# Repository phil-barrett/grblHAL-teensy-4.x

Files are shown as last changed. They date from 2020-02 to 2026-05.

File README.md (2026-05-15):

# grbl-teensy-4
GRBL Breakout Boards for Teensy 4.x Uses the [grblHAL Teensy 4 version](https://github.com/grblHAL/iMXRT1062).
# Resources for grblHAL, T41U5XBB and related CNC topics
[Resources](https://www.grbl.org/resources)

## Nov 12, 2025.  V2.20 is now available.
Upgraded to AHCT drivers.
Upgraded to EL3H7 optoisolators.
Added board level configuration to support spindle sync. See [user manual](https://github.com/phil-barrett/grblHAL-teensy-4.x/blob/master/T41U5XBB%20User%20Manual.pdf) for details.
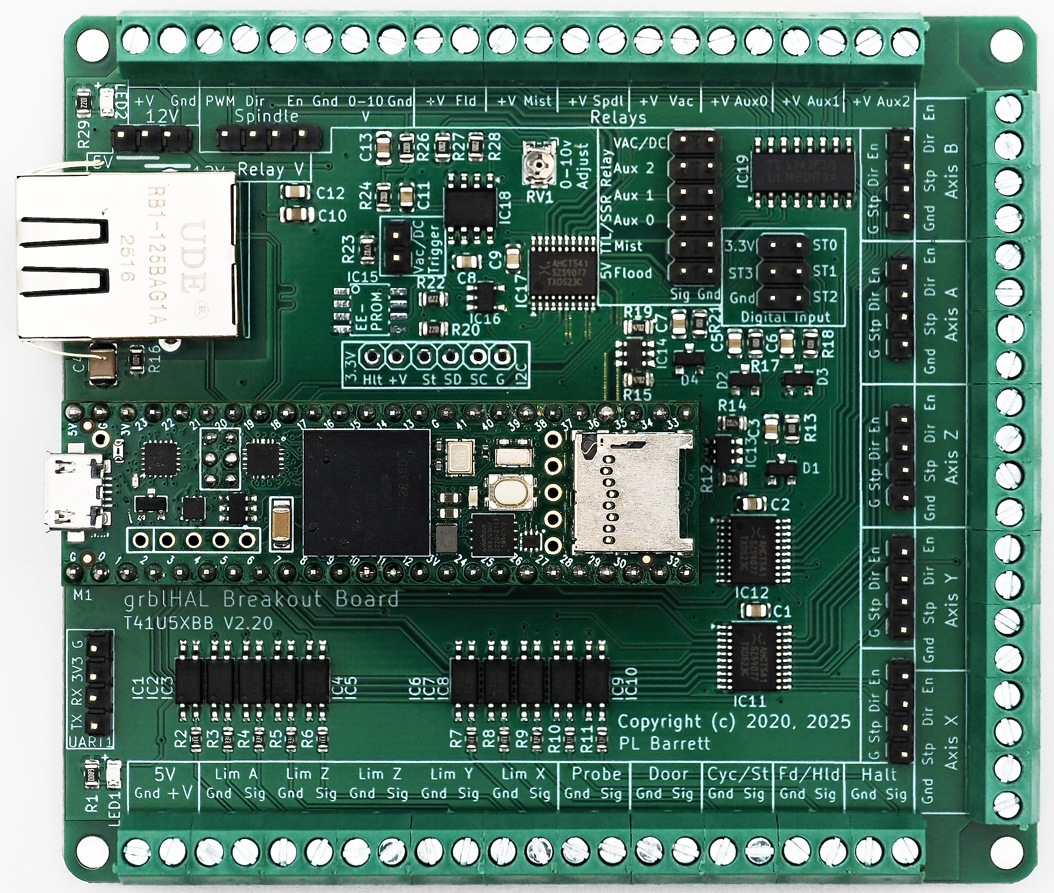
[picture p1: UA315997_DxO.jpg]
.

[Available for purchase on my store.](https://brookwood-design-77.myshopify.com/)

## Aug 20, 2025.  V2.10 is now available.
Trimmer potentiometer moved onto PCB, unneeded features removed and some cosmetic changes.  Now using KiCAD instead of Eagle. V2.11 is coming but is functionally the same as V2.10 (minor slik screen changes).  [User Manual](https://github.com/phil-barrett/grblHAL-teensy-4.x/blob/master/T41U5XBB%20User%20Manual.pdf) updated. 

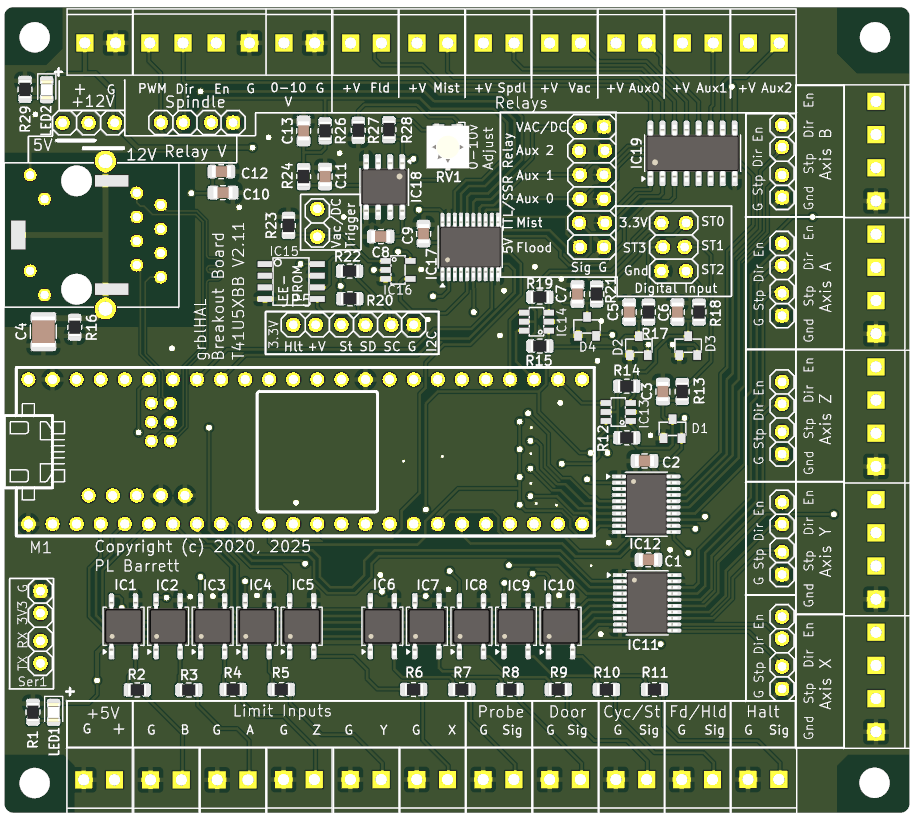
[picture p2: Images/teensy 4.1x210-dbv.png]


## Oct 15, 2020.  V2.09 is now available.
A small number of changes, mostly cosmetic. Also added mounting holes for I2C and Serial I/O daughter boards. 
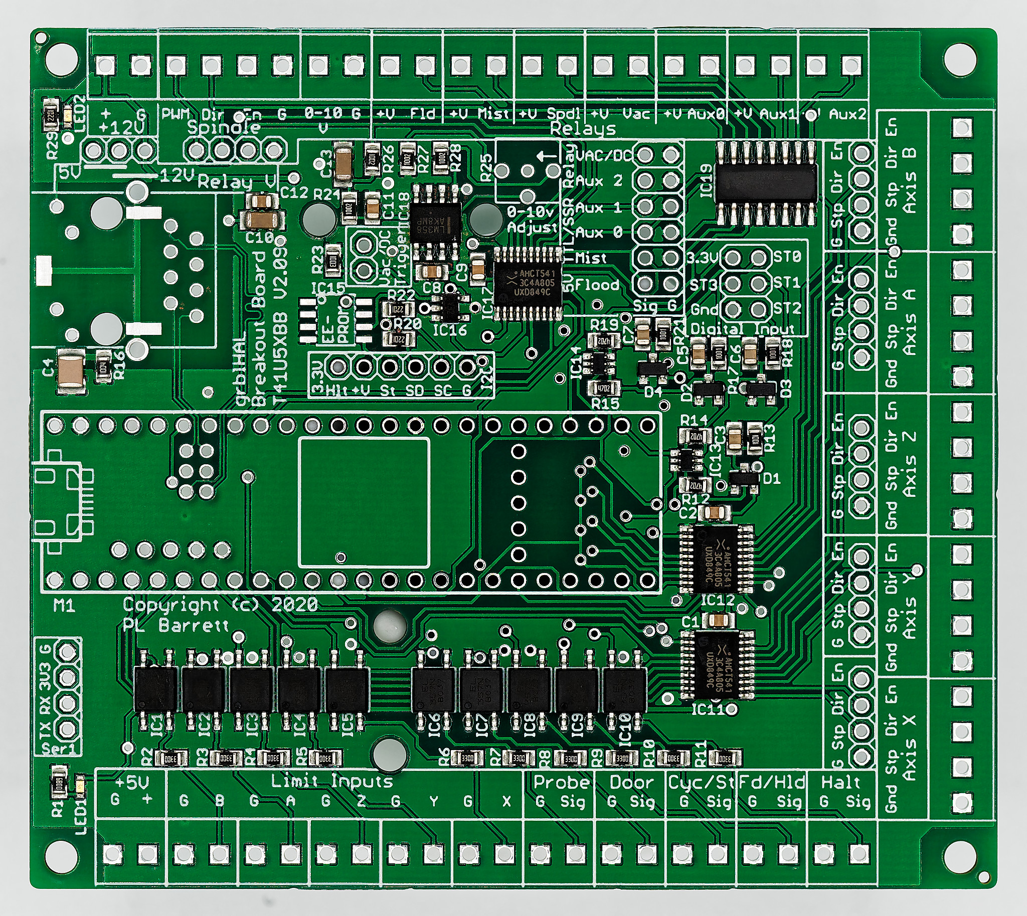
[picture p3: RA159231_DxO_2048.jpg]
T4.1 BreakuoutBoard V2.09 Unkit PCB


## Sept 29, 2020. Ethernet Support Added
grblHAL support for Ethernet is now pretty solid.  I have updated the [User Manual](https://github.com/phil-barrett/grblHAL-teensy-4.x/blob/master/T41U5XBB%20v207.pdf) to include instructions on using Ethernet. 

## June 28, 2020. New Versions!
I have finished 2 new 5 axis versions based on the Teensy 4.1. One supports an Ethernet interface and the other supports a USB interface. I will be making a few "Unkit" boards avalable. These have all the surface mount components installed (with the execption of the EEPROM IC). Teensy 4.1 not included. 

The "Unkit" board.
T4.1 BreakuoutBoard Unkit Version
T41U5XBB - Fully populated USB based version.  
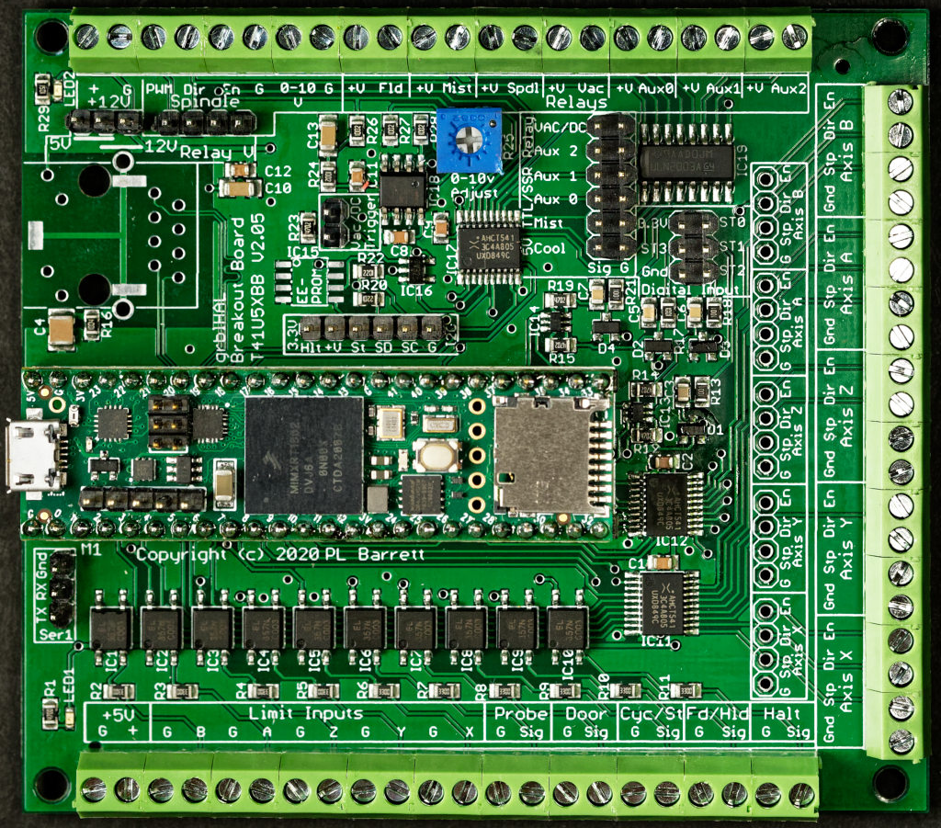
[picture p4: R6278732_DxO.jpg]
T4.1 BreakoutBoard T4.1 USB Breakout Board - T41U5XBB


T41E5XBB - Fully populated Ethernet version
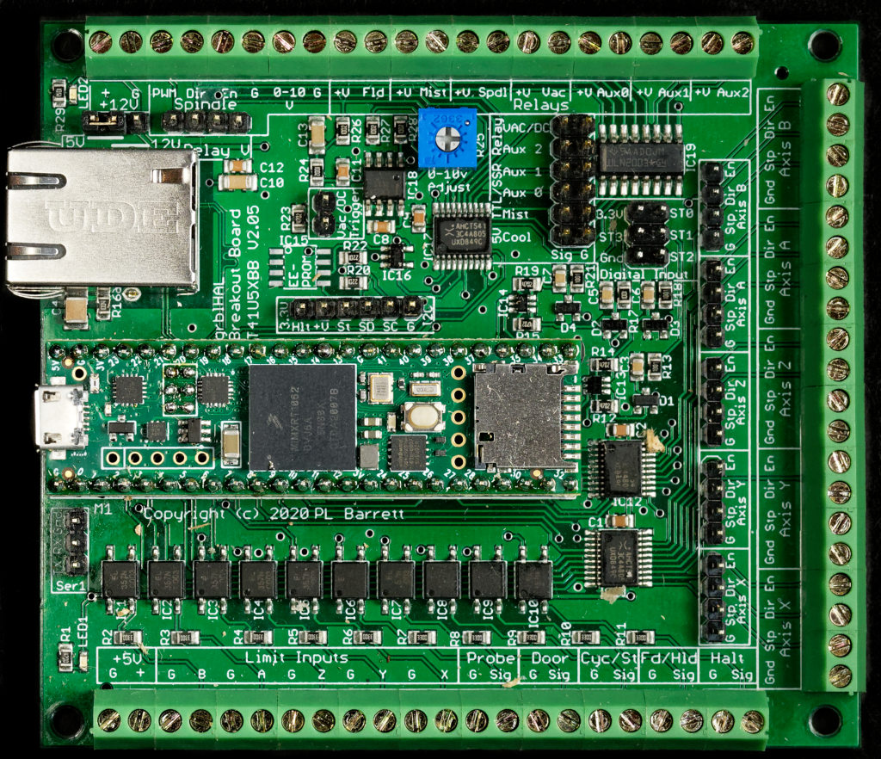
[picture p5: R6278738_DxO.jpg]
T4.1 BreakoutBoard T4.1 Ethernet BreakoutBoard - T41E5XBB


Lots of new features!
## Features
  * 5 Axis control outputs – 5V compatible.
  * Independent enables for each axis.
  * 10 Opto-isolated inputs including standard GRBL controls and limits switches for all axes.
  * 7 Relay Outputs – Spindle, Mist Coolant, Flood Coolant, Dust Collector and 3 auxiliary relays. Each output can control a relay coil directly or 5V TTL (SSR compatible) devices.
  * Dust Extraction relay support. Activated by spindle enable.
  * Separate control of Dust Collector relay via pin header.
  * Relay coil voltage switchable between 5V and 12V. 
  * Standard GRBL spindle control outputs – 5V compliant.
  * 0-10V spindle control output.
  * Screw Terminals for reliable connections available for most I/O.
  * 4 Digital Inputs – EMI protected, 15.9KHz low pass filter, Schmitt Trigger.
  * I2C header.
  * EEPROM footprint for SOIC8 devices.
  * LED indicators for 5V and 12V.
  * USB interface.
  * Ethernet interface. (T41E5XBB only)
  * Serial I/O Header

## Firmware
Prebuilt versions of grblHAL are available to directly load into the Teensy 4.1 [Follow the instructions here.](https://github.com/phil-barrett/grblHAL-teensy-4.x/blob/master/prebuilt.md)

## Documentation
### Schematic
The two versions currently share a common schematic and PCB layout. This may not be the case in the future. [Schematic is here.](https://github.com/phil-barrett/grbl-teensy-4/blob/master/v2.07%20schematic.pdf)

### Manual
The [User Manual is available here.](https://github.com/phil-barrett/grbl-teensy-4/blob/master/T41U5XBB%20v207.pdf)

### Bare PCB from OSHPark
[Available here](https://oshpark.com/shared_projects/QWr3OZUe) This is fairly expensive. For a less costly approach, you can use the Gerber files below to order from more cost effective fabs.

### Gerbers
[Gerbers are available here.](https://github.com/phil-barrett/grbl-teensy-4/blob/master/teensy%204.1x207.zip) Board size is 85 x 96 mm, 2 layer, 1.6 mm thickness.

### Build Guide
A brief guide to building grblHAL from source [for the breakout board is here](https://github.com/phil-barrett/grbl-teensy-4/blob/master/grblHAL%20Build%20Guide.pdf).

## Previous Version
T4 Breakout Board

## Features:
  * 4 Axis control outputs – 5V Compatible.
  * 8 Opto-isolated inputs.
  * Full spindle control outputs – 5V compatible.
  * 0-10V spindle control output.
  * 7 Relay Outputs.
  * Relay voltage switchable between 5V and 12V. 
  * Dust Extraction relay output slaved to spindle.
  * Screw Terminal I/O for reliable connections.
  * I2C header.
  * EEPROM footprint for SOIC8 devices.
  * LED indicators for 5V and 12V.

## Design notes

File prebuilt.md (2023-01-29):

## Prebuilt Firmware

### Prebuilt Firmware depreciated
With advent of the Web Builder, it is very easy to build custom versions of grblHAL firmware.  As such, there is no need for prebuilt versions. We will leave the current files available but highly recommend moving to the [grblHAL Web Builder](http://svn.io-engineering.com:8080/). For more information, take a look at a brief [tutorial on the grblHAL Web Builder](https://www.grbl.org/single-post/using-the-grblhal-web-builder).

### Using the Web Builder
Some Web Builder configuration files are [located here](https://github.com/phil-barrett/grblHAL-teensy-4.x/blob/master/iMXRT1062_T41U5XBB-files.zip). Download and extract the file that reflects your machine. Use the Load Board button to load the .json file. If one does not meet you exact needs, choose the one that is closest and modify it.

Here are the configuration files that are available:

iMXRT1062_T41U5XBB-3X.json - 3 Axis

iMXRT1062_T41U5XBB-3X-qangY.json - 3 Axis, Gang Y

iMXRT1062_T41U5XBB-3X-AutoSqY.json - 3 Axis, Auto-Square Y

iMXRT1062_T41U5XBB-3X-AutoSqY-SDCard-Keypad.json - 3 Axis, Auto Square Y, SDCard, Keypad

iMXRT1062_T41U5XBB-4X.json - 4 Axis

iMXRT1062_T41U5XBB-4X gangY.json - 4 Axis, Gang Y

iMXRT1062_T41U5XBB-4X-AutoSqY.json - 4 Axis, Auto-Square Y

iMXRT1062_T41U5XBB-4X-AutoSqY-SDCard-Keypad.json - 4 Axis, Auto-Square Y, SDCard, Keypad

iMXRT1062_T41U5XBB-5X-SDCard-Keypad.json - 5 Axis, SDCard, Keypad

Depreciated text follows.
### Available Versions
These are found in [configurations.zip](https://github.com/phil-barrett/grblHAL-teensy-4.x/blob/master/configurations.zip).   There are no USB only versions anymore.  These versions all work with USB or Ethernet. At this time, we do not recommend using the compat versions - you should use one of the many GCode Senders that work with grblHAL. If you need compatibility mode and other options, you will need to install the source from github and build it.

"3X qei" - 3 Axis, Aux Relays, Quadrature Encoder

"3X qangY qei" - 3 Axis, Aux Relays, Quadrature Encoder

"3X qangY AutoSq qei" - 3 Axis, Aux Relays, Quadrature Encoder

"3X qangY AutoSq qei SDCard Keypad" - 3 Axis, Aux Relays, Quadrature Encoder

"3X compat" - 3 Axis, no options, compatibility with older senders.

"4X qei" - 4 Axis, Aux Relays, Quadrature Encoder

"4X gangY qei" - 4 Axis, Aux Relays, Quadrature Encoder

"4X gangY AutoSq qei" - 4 Axis, Aux Relays, Quadrature Encoder

"4X gangY AutoSq qei SDCard Keypad" - 4 Axis, Aux Relays, Quadrature Encoder

"4X compat" - 4 Axis, no options, compatibility with older senders.

"5X qei SDCard Keypad" - 5 Axis, Aux Relays, Quadrature Encoder

"5X compat" - 5 Axis, no options, compatibility with older senders.

### Options
nX - number of axes

gangY - Y Motor is ganged with A (if 3 Axis) or B (if 4 Axis)

qei - Quadrature encoder on digital inputs. Supports spindle and feed rate override.

Compat - Sender compatibility.  disables new features of grblHAL and maintains compatibility with senders.

SDCard - SDCard support

Keypad - keypad support

More options will be added in the future.

### Loading Firmware onto a Teensy 4.1
Follow these basic steps:
1. Download the [firmware configurations file](https://github.com/phil-barrett/grblHAL-teensy-4.x/blob/master/configurations.zip) and extract the contents.
2. Select the .hex file that coresponds to the features you will use.
3. Obtain the Teensy Loader for your platform.
4. Use the loader to load the .hex file into your Teensy.

See the platform sections for details and hints.

#### Windows 
Download Teensy.exe from the [PJRC Website here](https://www.pjrc.com/teensy/loader_win10.html). The page may say Windows Vista but it works for all recent Windows versions.
Plug in your Teensy 4.1 via USB. Find Teensy.exe and run it.  It should open as a small window. In File/Open HEX File, select and open the .hex file you want and press OK. Then, press the button on the Teensy 4.1. You are ready to test it now. 

#### Macintosh OS X
Macintosh instructions [are here](https://www.pjrc.com/teensy/loader_mac.html). Plug in your Teensy 4.1 via USB. Follow the instructions to install and run the loader. It should open as a small window. Then, from the File name, choose "Open HEX File" and open the .hex file you want and press OK. Select "Program" from the "Operations" menu, or click the Program button on the tool bar. It should display a brief loading message. You are ready to test it now

#### Linux
Instructions for Ubuntu [are here](https://www.pjrc.com/teensy/loader_linux.html). Other Linux versions work though you will need to build the loader for your platform.  The [instructions and links to the github repository are here.](https://www.pjrc.com/teensy/loader_cli.html)

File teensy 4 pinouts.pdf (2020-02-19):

Teensy 4.0 GRBL Pin Assignment working document V 0.2

Goals:
1. Common Function on TH Pins for easy prototyping/testing. Simple machine should be possible with TH pins only.
2. Less Common Function of SMT “Back Side” Pins
3. Grouping of similar functions on nearby pins to simplify usage and PCB layout.

Issues/questions:
1. No onboard EEPROM. Use EEPROM emulation? How frequently does EEPROM get written? See (alt) Pin assignment.
2. Does USB use Ser 1? Pins need to be reserved?
3. Pin 13 is LED, output only. Currently on spindle enable. Is there a better use for that pin as a diagnostic?
4. Stepper enable is often unused in simple machines. Move that to back side to free up a TH pin?

Standard vs alternate assignment. Most pin assignments are the same for both. Main difference is the use of I2C channels on the through hole pins.
Through Hole Pins
Pin | Standard assignment | Alternate assignment
0 | Reserved RX1 | Reserved RX1
1 | Reserved TX1 | Reserved TX1
2 | Step X | Step X
3 | Dir X | Dir X
4 | Step Y | Step Y
5 | Dir Y | Dir Y
6 | Step Z | Step Z
7 | Dir Z | Dir Z
8 | Step A | Step A
9 | Dir A | Dir A
10 | Stepper Enable 0 | Stepper Enable 0
11 | Spindle Dir | Spindle Dir
12 | Spindle Enable | Spindle Enable
13 LED | Spindle PWM | Spindle PWM
14 | Reset/Abort | Reset/Abort
15 | Probe | Probe
16 I 2C 0 | Feed/Hold | I2C SCL ch 0
17 I 2C 0 | Cycle Start | I2C SDA ch 0

18 I 2C 1 | Mist Enable | I2C SDA ch 1
19 I 2C 1 | Flood Enable | I2C SCL ch 1
20 | Lim X | Lim X
21 | Lim Y | Lim Y
22 | Lim Z | Lim Z
23 | Lim A | Lim A

Back Side SMT Pins
Pin | Function assignment | Alternate assignment
24 I2C 2 | I2C SCL ch 2 | Feed/Hold
25 I2C 2 | I2C SDA ch 2 | Cycle Start
26 | Step B | Step B
27 | Dir B | Dir B
28 | Lim B | Lim B
29 | Door | Door
30 | Stepper Enable 1 | Stepper Enable 1
31 | Relay 5 | Relay 5
32 | Relay 6 | Relay 6
33 | GPIO 1 | Relay 7
34 | Stepper Enable 2 | Stepper Enable 2
35 | Stepper Enable 3 | Mist Enable
36 | Stepper Enable 4 | Flood Enable
37
38
39

Simple Machine Definition

This section defines the functions needed to build a simple CNC/Laser machine. The goal is to be able to do this only with through hole pins. This allows easy prototyping and testing.

Note that strictly speaking, Stepper Enable is unnecessary and Feed/Hold, Cycle Start are often omitted in basic machines. For Lasers, I believe Spindle pins are used for control.

Step X | Stepper Enable 0 | Lim Y
Dir X | Spindle PWM | Lim Z
Step Y | Spindle Enable | Lim A

Dir Y | Reset/Abort | Feed/Hold
Step Z | Probe | Cycle Start
Dir Z | Lim X

Note this is somewhat stating the obvious but I think it worthwhile to have written down.

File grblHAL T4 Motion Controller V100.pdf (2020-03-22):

## grbl/HAL Teensy 4.0 Motion Controller

V1.00

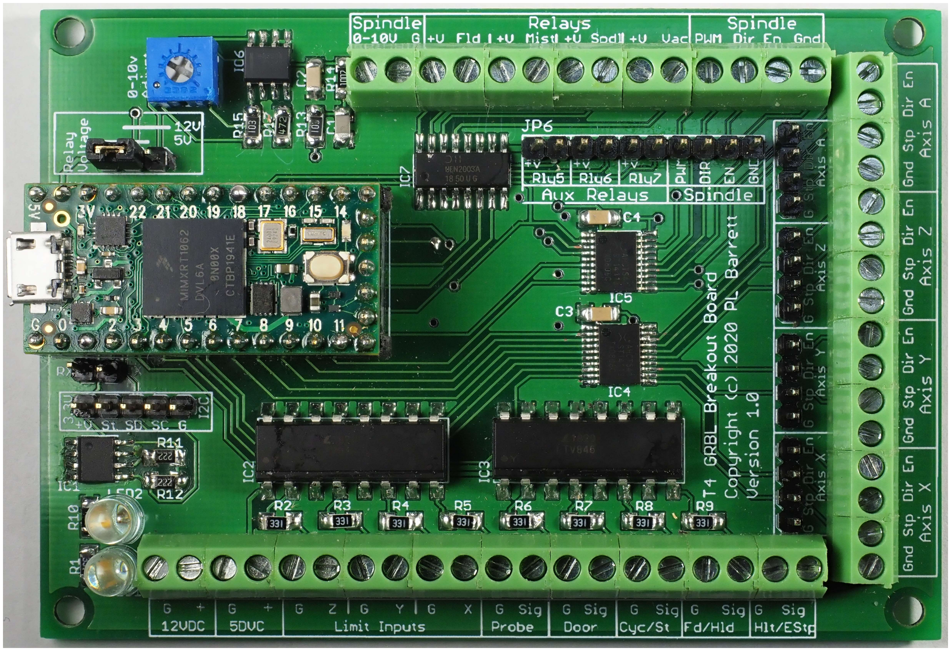
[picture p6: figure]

This document describes V1.00 of the grbl/HAL Teensy 4.0 Motion Controller.

### Features:

- 4 Axis control outputs – 5V Compatible.
- 8 Opto-isolated inputs.
- 7 Relay Outputs.
- Relay voltage switchable between 5V and 12V.
- Screw Terminal I/O for reliable connections.
- I2C header.
- EEPROM footprint for SOIC8 devices.
- Full spindle control outputs – 5V CMOS compatible.
- 0-10V spindle control output.
- Dust Extraction relay output slaved to spindle.
- LED indicators for 5V and 12V.

Stepper Driver outputs.
There are 4 sets of standard GRBL stepper driver outputs: X, Y, Z and A axes. Each has 3 pins: step, direction and enable. Each are 5V compatible and capable of driving opto-isolated stepper driver inputs. Each axis has a set of screw terminals as well as pin headers (0.1”/2.54mm spacing).

Limit Pins.
There are X, Y and Z opto-isolated limit pins available via screw terminals.

Input Pins.
Standard GRBL input pins are supported via screw terminals: Feed/Hold, Cycle/Start, Halt/Stop and Safety Door open. These are opto-isolated.

Copyright © 2020 P. L. Barrett

Probe Input
Probe input is opto-isolated and is available via screw terminals.

Spindle Control.
Screw terminal and pin header outputs for Spindle Enable, Spindle Direction and PWM signals. These are 5V CMOS logic compatible. There is a relay output for the spindle. See Relay section for more details. In addition, 0-10V output for spindle control is provided via a screw terminal.

Relay outputs.
Standard GRBL Flood and Mist relay outputs are supported via screw terminals. Spindle relay output via a screw terminal is supported and controlled by Spindle Enable. In addition, a separate screw terminal relay output for Dust Collection is slaved off the Spindle Enable output.

3 additional relay outputs are supported via pin headers and used via M62-M65 grbl/HAL pin control.

All relay outputs are capable of directly driving relay coils. Each relay driver is capable of up to 100 mA. All 7 are limited to 500 mA in total though above 250 mA, forced air cooling is recommended.

All relays drivers have open collector outputs.

Relay voltage is selectable between 5 and 12V via pinheader labeled Relay Voltage in the upper left corner of the PCB.

I2C Header
An I2C header is provided. 3.3V only, there is no translation to/from 5V. In addition a strobe line from Teensy 4.0 pin 33 is provided on the header. Currently, only a limited number of devices are supported. Check the grbl/HAL github site for more details.

### PCB Assembly

Not all components are required. See Optional Components section for more information.

Assemble the PCB in the following order:
1. Use a flux pen on all pads.
2. Solder the smallest SMD components first – resistors, capacitors.
3. SMD ICs next. Take care with IC4 and IC5 when soldering. Draw the soldering iron along the legs, not perpendicular to them as they easily bend.
4. Now is a good time to verify that all leads are properly soldered. Visual inspection with a magnifier is a good idea. Electrical continuity testing is very helpful – leads that look OK are sometimes not.
5. Mount and solder trimmer resistor R16 and the LEDs next. LED anode goes towards the top of the board (cathode connects to resistor). Trim excess leads.
6. Install the Teensy 4.0 – sockets or actual T4 with headers. See Teensy 4.0 Mounting Options for more information. Now is a good time to test the board before the headers and terminals are installed, making changes harder.
7. Mount and solder any pin headers that you will be using. See diagram xxx for options. Use tape to hold them in place while soldering. Solder an end pin and then adjust for proper alignment. Finish by soldering the rest of the pins.
8. Mount and solder screw terminals. Assemble a complete row, insert and solder an end pin. Then solder the pin at the other end, making sure the row is properly aligned. Then solder remaining terminals while ensuring that the row is straight.

Optional Components.

Many components are optional. Refer to the following diagram.

Notes:
- RX, TX and I2C headers are optional. Install if you need to use an alternate USB connection. Grbl/HAL will work correctly without either header installed.
- EEPROM is optional, Install if you need to use an external EEPROM. Grbl/HAL will work correctly without it.
- Power indicator LEDs are optional. Useful to see if you have power. Grbl/HAL will work correctly without it.
- 0-10V Spindle control is optional. Use if you are using a VFD controlled spindle. Grbl/HAL will work correctly without it if you are manually controller your spindle. We recommend installing the screw terminals as they are hard to add later.
- Relays are optional. The grbl/HAL Teensy 4 Motion Controller is capable of driving relay coils directly. It is recommended that you install the screw terminals even if you don't initially plan on using them. Installing later can be difficult. See note on Vacuum/Dust Collector relay below. But, Grbl/HAL will work correctly without any relays.
- A Axis is optional if you don't have one in your CNC machine.
- Safety Door alarm. Install if you have an enclosure for your CNC machine with a Safety Door sensor. See note about backside pins in the Teensy 4.0 mounting options section below. Grbl/HAL will work correctly without it but see Testing section for disabling the alarm.

### Teensy 4.0 Mounting Options

The Teensy 4.0 comes with 3 sets of pins:
- The T4 has through holes around the perimeter. Typically header pins are soldered into them. The best way to ensure the pins are soldered in straight is to insert them into a solderless breadboard, place the Teesny 4.0 on top of them and solder in place. Take care when prying the assembly off the breadboard. The Teensy 4.0 should like the picture below.
- There is a set of SMD pads for pins 24 through 33 on the bottom. PRJC calls them Backside Pins. We recommend you not bother with them unless you are using a Safety Door Open Sensor, Relays 5 through 7 or the I2C header. If you wish to use them, there are surface mount pin headers that will work. These are difficult to solder because there a number of 402 SMD components close by and it is easy to knock them off. The author of this document has a dead Teensy 4.0 to prove that point. It is possible to use pogo pins though this has not been tested.
- The 3rd set of SMD pads, pins 34 through 39, are unused.

Mounting the Teensy 4.0 on the grbl/HAL Motion Controller PCB can be done in one of two ways:
- Solder directly. This is more reliable though commits the Teensy 4.0 to this application. Install pin headers as shown below and then insert the assembly in place on the PCB and solder. This is the recommended approach to ensure reliability.
- Use pin sockets. These are generally reliable but in a high vibration environment can shake loose. Ensure that the pin headers are installed on the Teensy 4.0 as shown in the picture below. Place the sockets on the Teensy 4.0 (with the headers pins installed) and then insert into the PCB for soldering. Using tape to hold the Teensy 4.0 assembly in place, solder 1 pin at the end of each row, check the alignment and adjust as necessary. Once you are satisfied with the alignment, solder all the pins in place.

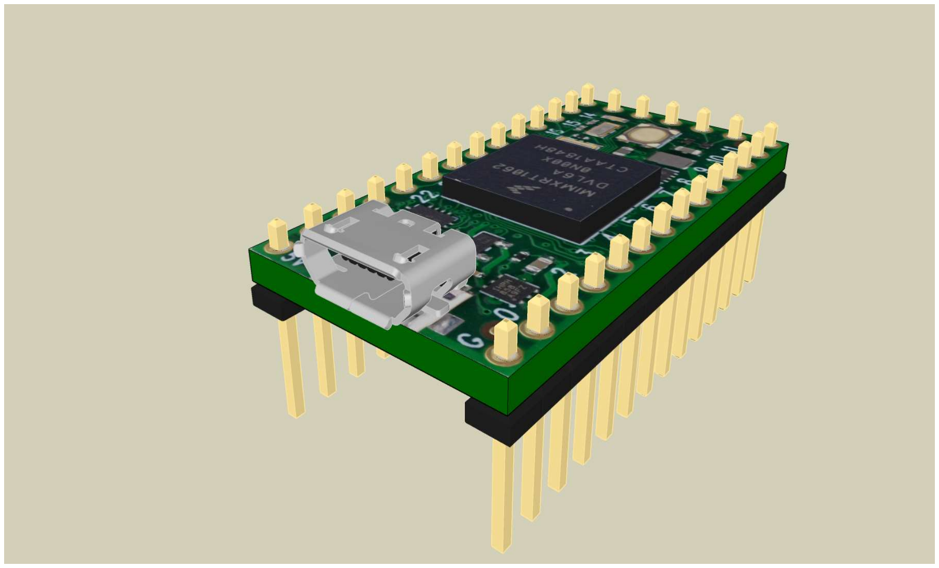
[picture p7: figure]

### Relay Voltage

Relay Voltage source is selectable between 5V fed by the USB host and 12V (or higher) provided via an external power supply. Use a “suitcase jumper” as indicated on the PCB to select the desired voltage. Note, if using more than 2 relays at 5V, we recommend you use an external 5V supply. To do so, you must disconnect VUSB feed on the Teensy 4.0. On the bottom side of the Teensy 4 in the upper right hand corner, when looking at it from the bottom, there is a trace to be cut. That separates Vin from the USB cable and allows 5V input via the screw terminal. See the info card that comes with the Teensy 4.0 or PJRC.COM for more information.

Relay coil voltage up to 48V is permissible and is applied at the input terminal labeled 12V. If using higher than 12V, we recommend changing resistor R1 to limit LED current to below 10 mA. For 24V, use 2.2K Ohm and, for 48V, use 4.7K Ohm. The user is responsible for ensuring that all relays are rated for the voltage they provide.

### Dust Extractor/Vacuum Control

An additional relay driver is provided to drive a dust extractor relay. It is slaved to the Spindle Relay – both are energized when the spindle is turned on (M3). In addition, this relay can be separately and independently controlled by a switch that connects the terminal labeled Vac to ground. The switch must be rated for 200 mA or more. This makes it easy to do clean up with the same shop vac used for dust extraction.

### Loading grbl/HAL

A prebuilt binary is available on github at https://github.com/phil-barrett/grbl-teensy-4. One can also download the source code at https://github.com/terjeio/grblHAL and build it.

### Testing

Your grbl/HAL Teensy 4.0 based Motion Controller is ready to be tested. Attach it to a PC via a USB cable and run a compatible GRBL sender application. We recommend this one: https://github.com/terjeio/Grbl-GCode-Sender Check for the most recent release.

Note, it you don't attach any switches, the system will come up in the alarm state. This is normal. If you are not using the Safety Door Alarm, in the Settings: Grbl tab, Invert control pins section, check the Safety Door box. This makes the system see the (nonexistant) Safety Door as closed.

### 0-10V output setup

The 0-10V circuit works by using an opamp to filter a 3.3V PWM signal and amplify it to 10V. As such it needs 12V input which the user must provide. A second order filter with an aggressive low pass cut off frequency is used to provide a stable signal for the spindle controller.

Because source voltage level can vary, the gain of the op amp must be adjusted. To adjust:
- In the Settings: Grbl tab, set $30, Maximum Spindle Speed, to 1000.
- Send the following command to GRBL: M3 S1000. This turns on the spindle and causes the speed to be set to 100%. The LED on the Teensy 4 should light up.
- Connect a Volt Meter to the 0-10V output and G terminals.
- With a screwdriver, turn R16 until the voltage is as close to 10V as you can get. Anything in the range 9.990V to 10.010V is acceptable.

### Errata:

1. Silk screen legends for Relays 5 and 7 are reversed.
2. The TX, RX header is lacking a ground. Use one of the other terminals or pins marked Gnd or G if you wish to use serial I/O. Grbl/HAL doesn't use it though.
3. Silk screen marks for LED's Anode are missing.

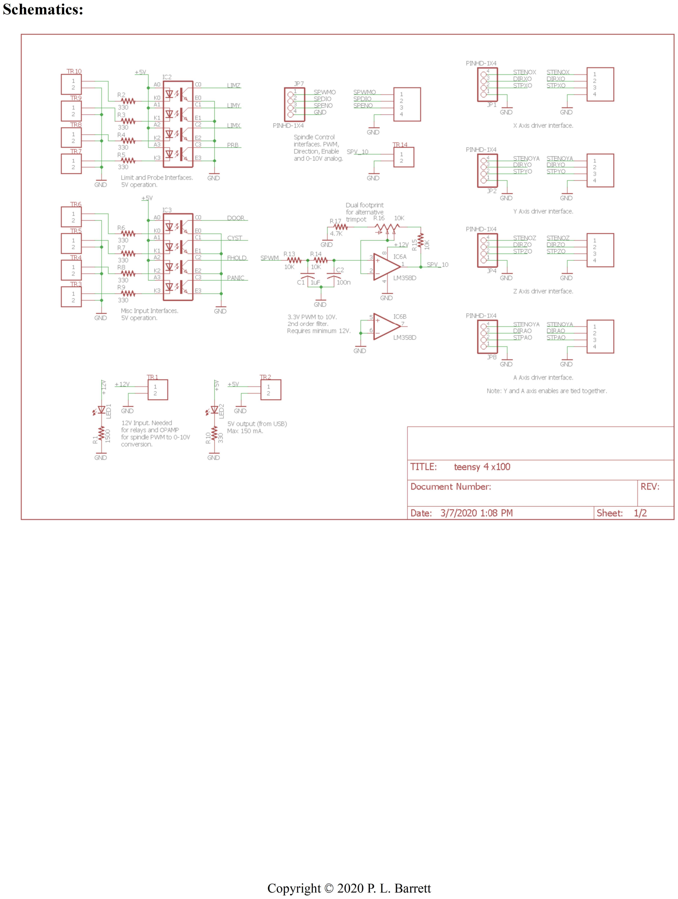
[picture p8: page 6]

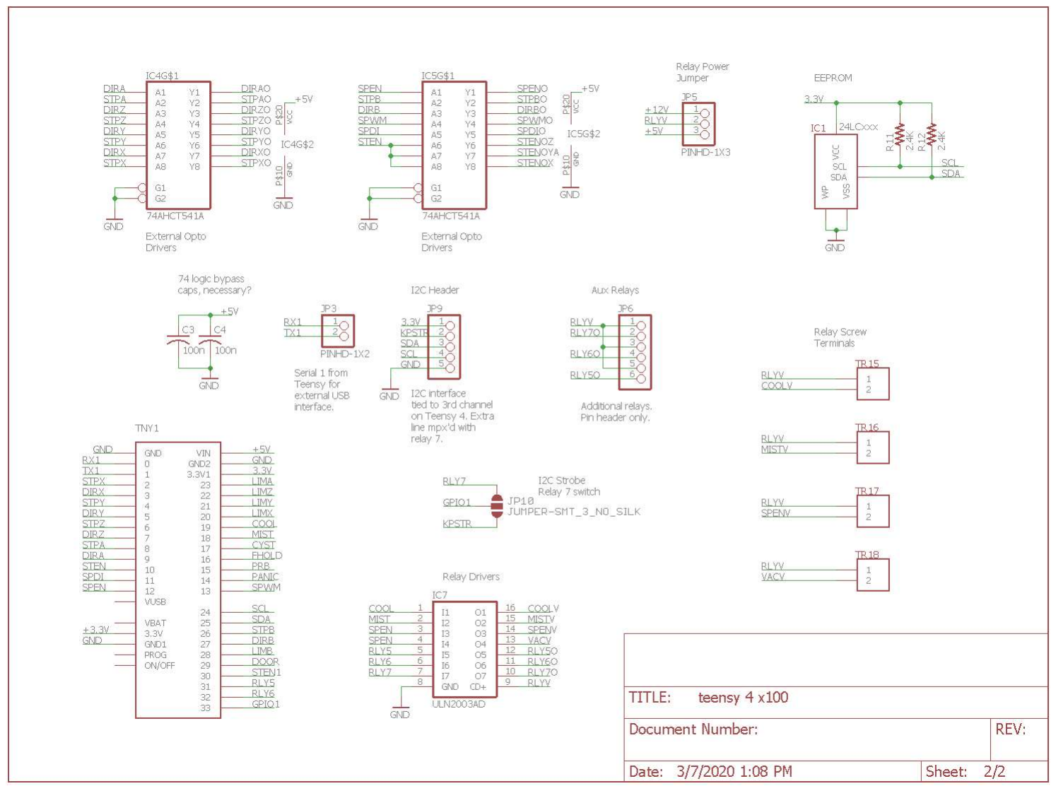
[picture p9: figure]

### Bill of Materials

Notes:
- The PCB has a dual footprint for the10K trimmer potentiometer and will accept 2 different footprints: 3 pins in a row with 0.1”/2.54 mm pitch or a triangular layout with the middle pin offset by 2.54 mm. The first footprint is used by more expensive multiturn trimmers and the second is very common and low cost. The BOM has the lower cost version. Also, you could use a 2K trimmer in place of the 10K.
- 3.5mm pitch screw terminals are fairly common and can be purchased from ebay/amazon/banggood/ali express.
- Pin headers are readily available from the same sources.
- Single row sockets are also readily available from the same sources though good quality ones are not that expensive. We recommend you use good quality sockets.
Part | Value | Number Package | Mouser Part Number | Cost | Unit total | notes
C1 | 1uF 25VDC | 1 | 1206 | 791-1206F105Z250CT | $0.10 | $0.10
C2 – C4 | 100n 25VDC | 3 | 1206 | 710-885012208058 | $0.11 | $0.33
IC1 | 24LC16 | 1 | SOIC-8 | 579-24LC16BT-E/SN | $0.34 | $0.34
IC2 – IC3 | LTV846S | 2 | DIL16-SMD | 859-LTV-846S | $0.68 | $1.36
IC4 – IC5 | 74AHCT541A | 2 | TSSOP20 | 771-74AHCT541PW-T | $0.40 | $0.80
IC6 | LM358D | 1 | SOIC-8 | 595-LM358ADRG4 | $0.36 | $0.36
IC7 | ULN2003AD | 1 | SO16 | 621-ULN2003AS16-13 | $0.48 | $0.48
LED1, LED2 | Green | 2 | LED, TH, T-1 (3 mm) | 859-LTL-4232 | $0.12 | $0.24
R1 | 1500 | 1 | 1206 | 660-RK73B2BTTD152J | $0.10 | $0.10
R2 – R10 | 330 | 9 | 1206 | 660-RK73B2BTTD331J | $0.10 | $0.90
R11 – R12 | 2.4K | 2 | 1206 | 660-RK73H2BTTD2401 | $0.10 | $0.20
R13 – R15 | 10K 1% | 3 | 1206 | 660-RK73H2BTTD1002F | $0.10 | $0.30
R16 | 10K trimmer | 1 | multiple | 3362P-1-103LF | $1.02 | $1.02 cheaper available
R17 | 4.7K 1% | 1 | 1206 | 660-RK73H2BTTD4701F | $0.10 | $0.10
TNY1 | 1 | TEENSY4.0 | $19.95 | $19.95 pjrc.com
Pinheaders | 36 | 2.54mm/0.1” pitch | varies | 0 multiple sources
TR1 – TR20 | screw terminal 25 | 3.5mm Pitch 2 pin | varies | 0 multiple sources
Total | $26.58
Sockets for Teensy | 2 | 14 pin 2.54mm pitch | 437-8018701410001101 | $1.20 | $2.40
Sockets for Teensy | 3 | 5 pin 2.54mm pitch | 437-8018700510001101 | $0.49 | $1.47
Backside Pin Header | 1 | 5x2 pin 2.54mm pitch | 571-5-146131-4 | $1.28 | $1.28

If not using backside pins, you only need 2 14 pin and one 5 pin sockets.

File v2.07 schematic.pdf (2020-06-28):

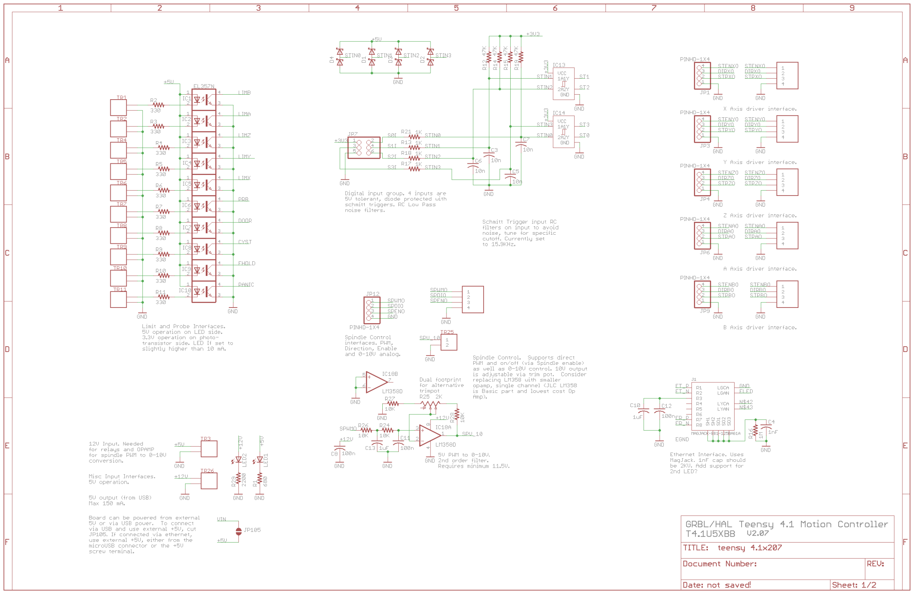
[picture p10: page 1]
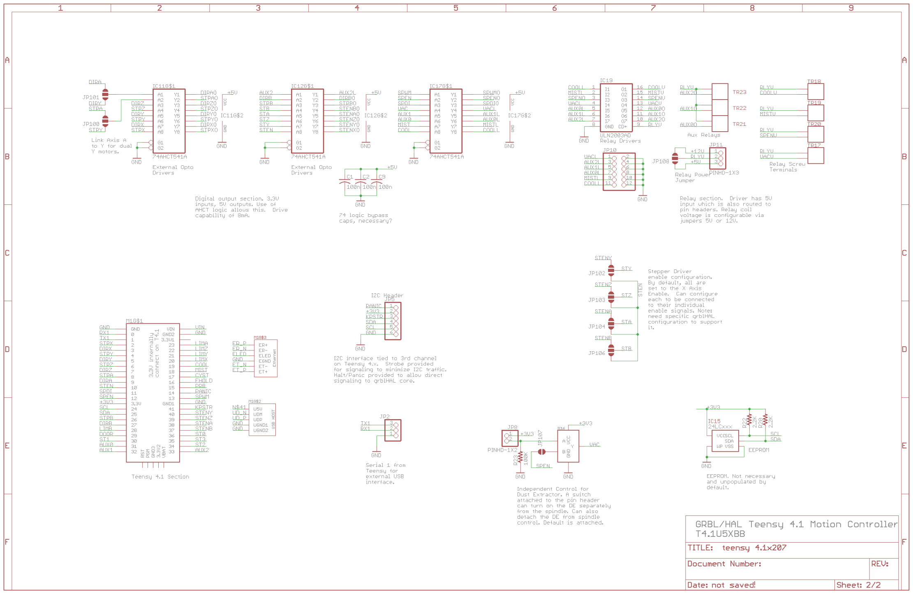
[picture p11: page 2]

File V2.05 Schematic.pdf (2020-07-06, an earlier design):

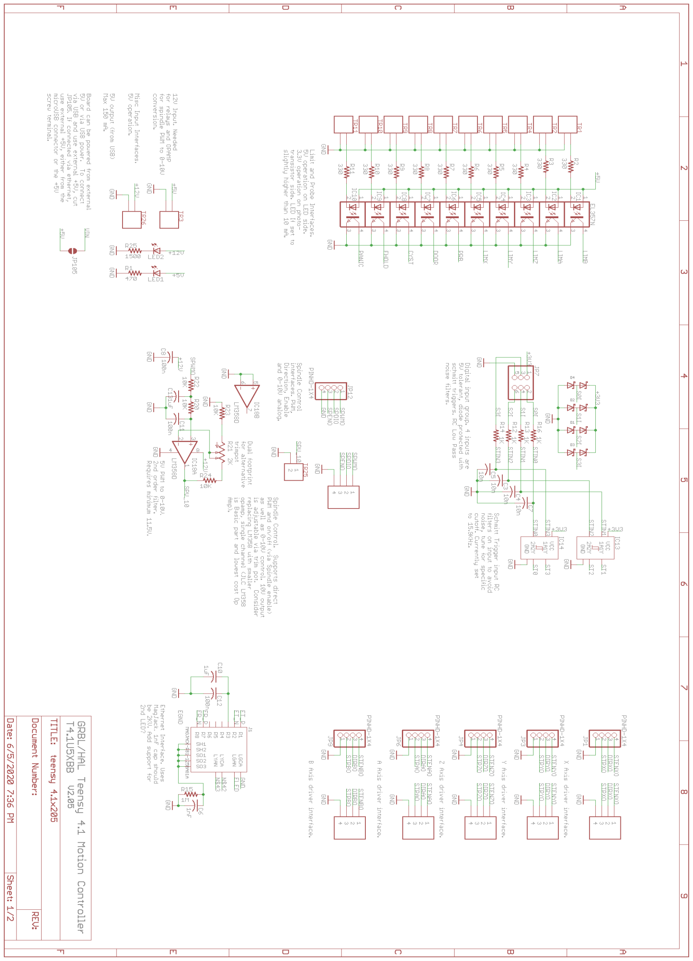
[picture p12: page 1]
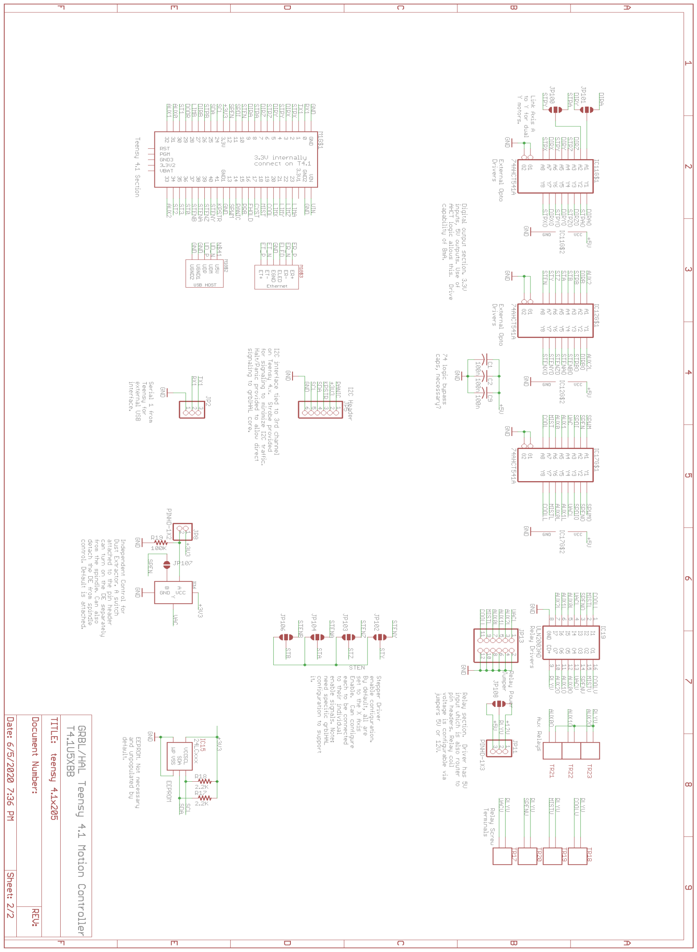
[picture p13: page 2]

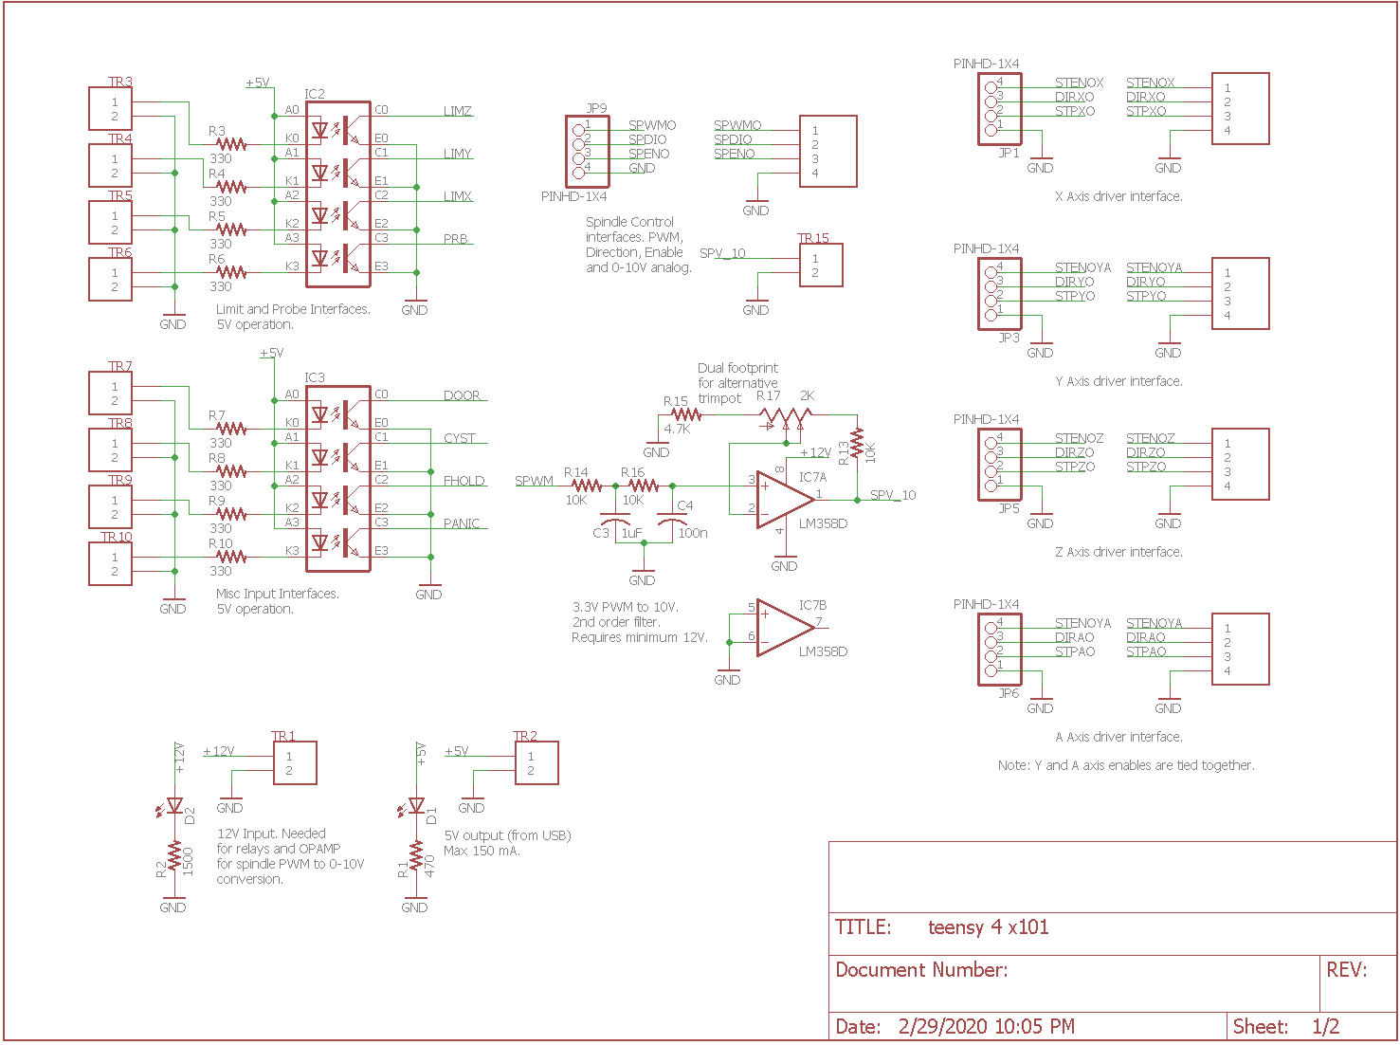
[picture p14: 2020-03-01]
schematic 1 of 2.png

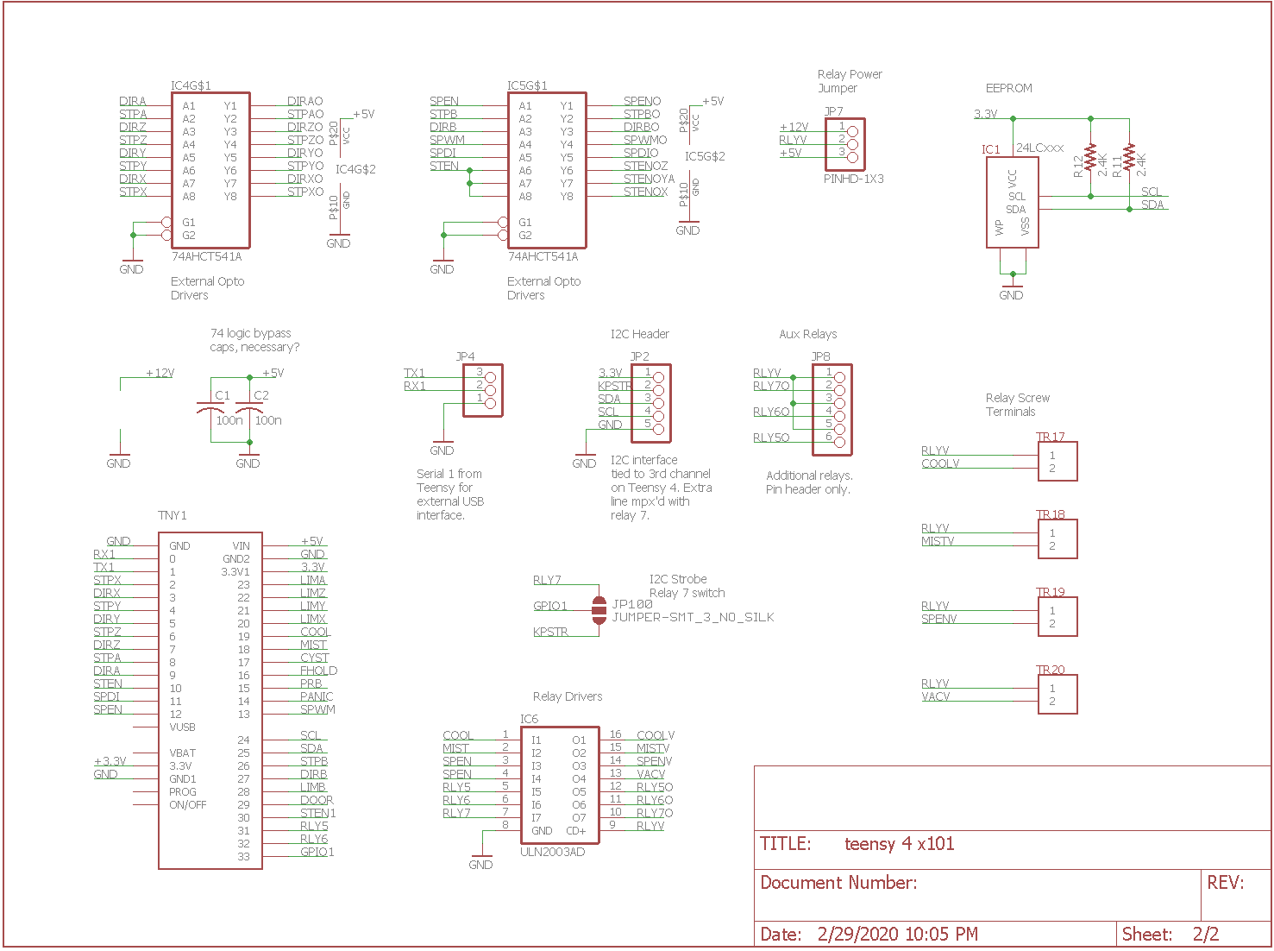
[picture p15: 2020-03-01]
schematic 2 of 2.png

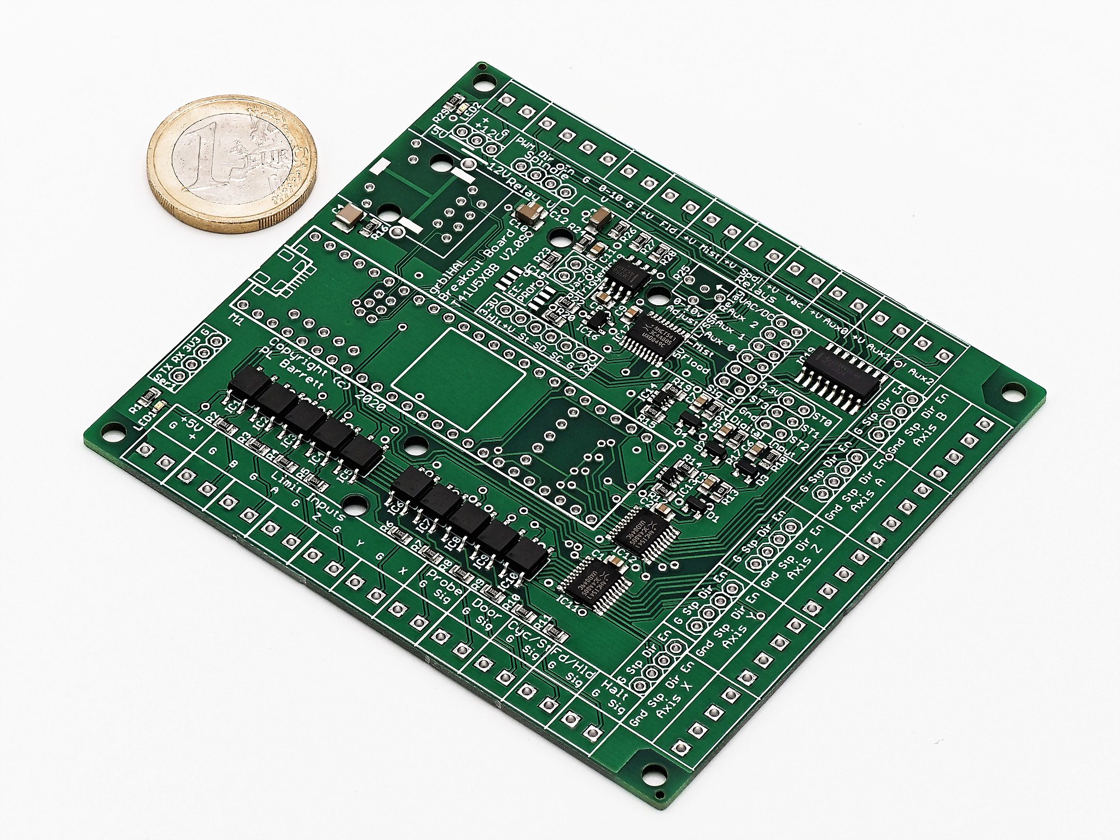
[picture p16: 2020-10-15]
RA159259_DxO_2048.jpg

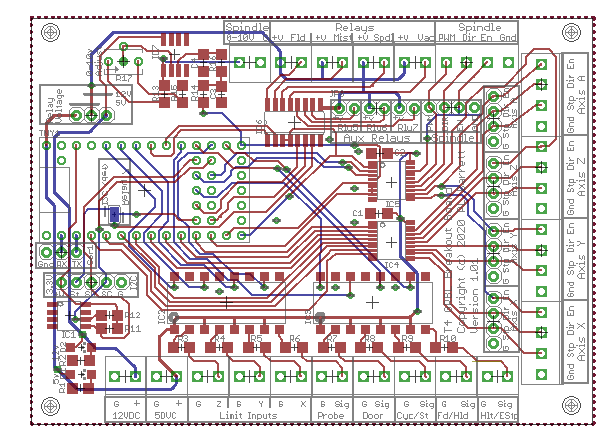
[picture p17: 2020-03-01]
PCB traces.png

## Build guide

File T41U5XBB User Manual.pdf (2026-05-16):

## grblHAL Teensy 4.1 Motion Controller Breakout Board T41U5XBB User Manual

Versions 2.07, 2.09. 2.10, 2.11, 2.20, 2.21

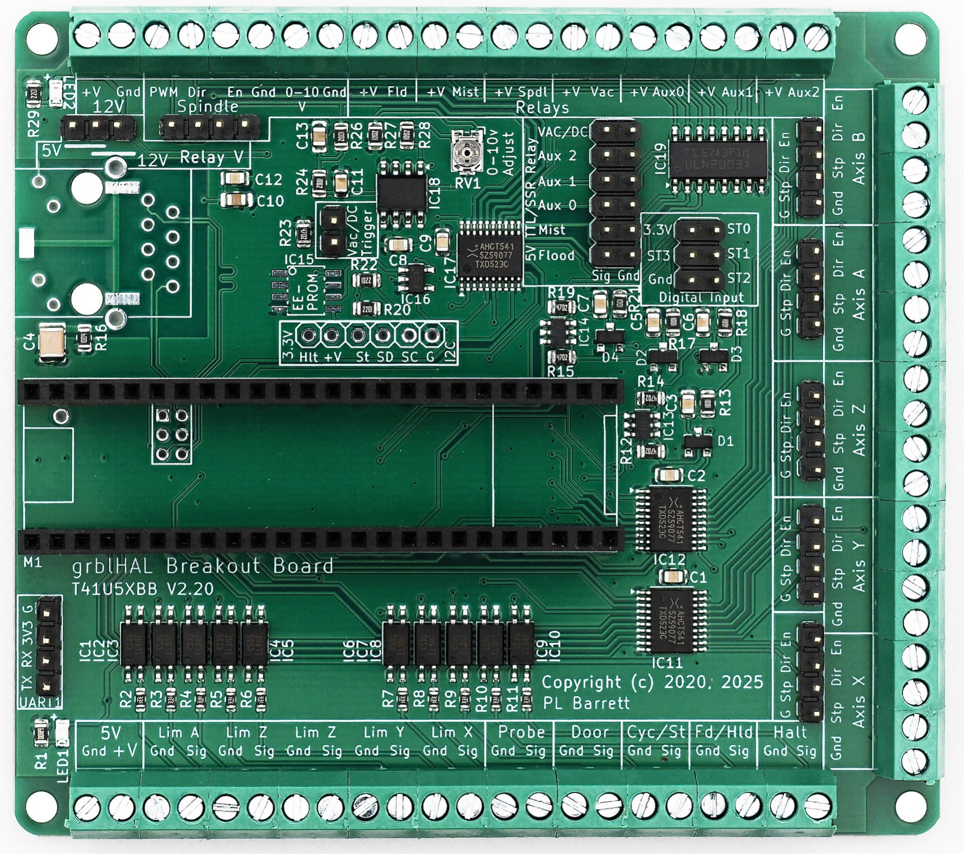
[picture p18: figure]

T41U5XBB – 5Axis, USB connected Breakout Board

Copyright © 2020, 2025 P. L. Barrett

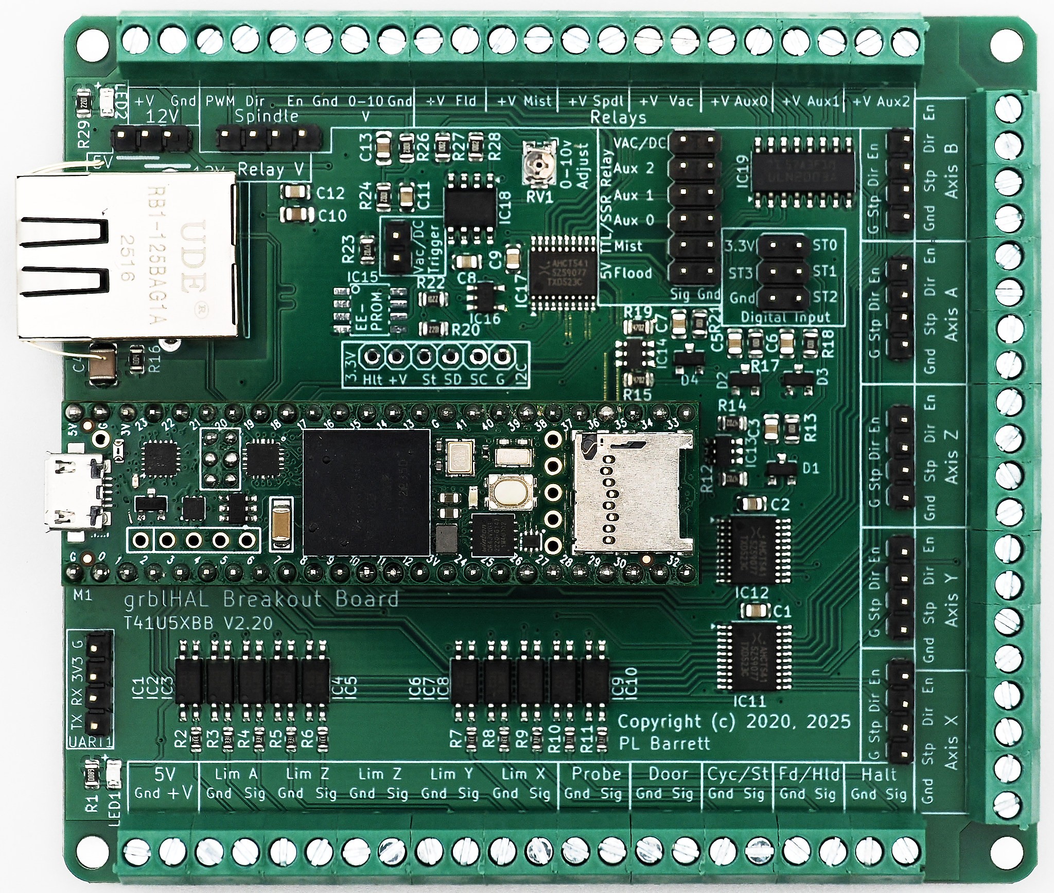
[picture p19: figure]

T41U5XBB – With Ethernet

### Features:

- 5 Axis control outputs – 5V compatible.
- Independent enables for each axis.
- 10 Opto-isolated inputs including standard grbl controls and limits switches for all axes.
- 7 Relay Outputs – Spindle, Mist Coolant, Flood Coolant, Dust Extraction and 3 auxiliary relays. Each output can control a relay coil directly or 5V TTL (SSR compatible) devices.
- Dust Extraction relay support. Activated by spindle enable.
- Separate control of Dust Collector relay via pin header.
- Relay coil voltage switchable between 5V and 12V.
- Standard GRBL spindle control outputs – 5V compatible.
- 0-10V spindle control output.
- Screw Terminals for reliable connections available for most I/O.
- 4 Digital Inputs – EMI protected, 15.9KHz low pass filter, Schmitt Trigger.
- Supports grblHAL Spindle Sync (V2.20 and later)
- I2C header.
- EEPROM footprint for SOIC8 devices.
- LED indicators for 5V and 12V.
- USB interface.
- Ethernet interface.
- Serial I/O Header

Stepper Driver outputs.
There are 5 sets of standard GRBL stepper driver outputs: X, Y, Z, A and B axes. Each has 3 pins: step, direction and enable. Each are 5V compatible and capable of driving opto-isolated stepper driver inputs. Each axis has a set of screw terminals as well as pin headers (0.1”/2.54 mm spacing).

Limit Pins.
There are 5 limit inputs: X, Y, Z, A and B. All are opto-isolated and available via screw terminals.

Control Input Pins.
Standard GRBL control input pins are supported via screw terminals: Feed/Hold, Cycle/Start, Halt/Stop and Safety Door open. These are opto-isolated.

Probe Input
Probe input is opto-isolated and available via screw terminals.

Spindle Control.
Outputs for Spindle Enable, Spindle Direction and PWM signals available via screw terminal and pin header. These are 5V TTL logic compatible. There are relay outputs for the spindle (direct relay coil and 5V TTL). See Relay section for more details. In addition, standard 0-10V output for spindle control is provided via a screw terminal.

Relay outputs.
Standard GRBL Flood and Mist relay outputs are supported via screw terminals. Spindle relay output via a screw terminal is supported and controlled by Spindle Enable. In addition, a separate screw terminal relay output for Dust Collection is activated by the Spindle Enable output.

3 auxiliary relay outputs are supported via screw terminals and used via M62-M65 grblHAL pin control.

All relay coil outputs are capable of directly driving relay coils. Each relay driver is capable of up to 100 mA. All 7 are limited to 500 mA in total. Above 250 mA, forced air cooling is recommended.

All relay coil drivers have open collector outputs.

Each relay also has a 5V TTL output that can be used to drive solid state relays, separate relay boards or other low voltage activated devices.

Relay coil voltage is selectable between 5 and 12V/24V via the pinheader labeled Relay Voltage in the upper left corner of the PCB or, alternatively, via a solder jumper on the bottom the PCB.

Schmitt Triggered digital inputs:
Four digital inputs are provided via a pin header. These have Shottky Diode protection and a low pass RC filter with an 15.9 KHz cutoff frequency. See the schematic for the specific circuit.

I2C Header
An I2C header is provided. 3.3V only, there is no translation to/from 5V and the inputs are not 5V tolerant. A strobe line from the Teensy 4.1 pin 33 is provided on the header. In addition, a line for an E-Stop signal is routed directly to the grbl Halt input. Currently, only a limited number of devices are supported. Check the grblHAL github site for more details.

### Versions

There are is only one version of this board. Ethernet is supported by adding the Ethernet MagJack – available via an optional kit. Part numbers are also provide for those that wish to source it themselves.

In both cases you need to load the appropriate version of grblHAL. See Loading Firmware section for details.

### External Connections

Power

12V, Input
Supply for relays and 0-10V output amplifier.

5V Input or Output
Supply for 5V logic and Teensy 4.1 when not power via microUSB connector. Can supply upt to 150 mA to off board devices.

Stepper motor, Output
5V signals.
Pin | Signal
G | Ground
Stp | Step Pulse. Positive.
Dir | Direction
En | Enable

Limit Switches, Input
One input for each axis. Opto-isolated, 5V.

Halt, Door, Cycle/Start and Feed/Hold, Input Opto-isolated, 5V.

Probe
Opto-isolated, 5V.

Spindle Group, Output.
PWM, Direction, Enable, Ground. This is a 5V group.
0-10V.

Relay Coil Group, Output
These are open collector sinks. They run at the selected relay voltage.
Flood, Mist, Spindle, Vac/Dust Collector, Aux0, Aux1, Aux2

Relay TTL Group, Output.
These are 5V, TTL compatible outputs suitable for SSR and powered relay modules. Flood, Mist, Vac/Dust Collector, Aux0, Aux1, Aux2.
Note: Enable in the Spindle Group is capable of driver SSRs and powered relay modules.

Vac/DC trigger.
External Switch to activate a vacuum or dust collector.

Digital Input
4 input pins, 3.3V and Ground. Schmitt Triggered input, diode protected and low pass filtered. See schematic for more details.
Pin | Signal
St0 | Schmitt Triggered, Low Pass Filtered (15.9KHz)
St1 | Schmitt Triggered, Low Pass Filtered (15.9KHz)
St2 | Schmitt Triggered, Low Pass Filtered (15.9KHz)
St3 | Schmitt Triggered, Low Pass Filtered (15.9KHz)
3.3V | 3.3VDC
Gnd | Ground

S0-S3 are 5V tolerant. Note that V2.05 is not 5V tolerant but V2.07 and later are.

I2C Header, Input/Output.

Pin | Signal
G | Ground
SC | I2C SCL
SD | I2C SDA
St | Strobe
+V | 3.3VDC, source by Teensy 4.1
Hlt | Halt Signal. Connected to the Halt input Teensy 4.1 pin.

### PCB Assembly

Not all components are required. See Optional Components section for more information.

Preparing the Teensy 4.1

See the blog post about building the T41U5XBB in pictures. (https://www.grbl.org/single-post/building-the-breakout-board)

Before installing components, you need to decide how you will connect the Teensy 4.1 to the breakout board. There are two approaches:
1. Use sockets to mount the Teensy to the breakout board. This is the preferred approach. It is more flexible but runs the risk of shaking loose in a moderate to high vibration environment.
2. Directly solder the Teensy to the breakout board. This is the recommended approach for high vibration environments. It makes for a much more secure connection. This is also easier than the socket approach if using Ethernet.

Materials for directly soldering. See BOM section for ordering numbers.
- 2 24 pin 0.1” pin-header strips. These can be obtained from numerous sources.
- 1 2x3 2 mm pin-header for the Ethernet connection.

Materials for socketing. See BOM section for ordering numbers.
- 2 24 pin 0.1” pin-header strips. These can be obtained from numerous sources.
- 2 24 pin 0.1” sockets.
- 1 riser 2x3 2 mm pin header. (For Ethernet)
- 1 2x3 2 mm socket. (For Ethernet)

The T41U5XBB is provided with all surface mount components soldered in place. You are responsible for installing the through-hole connectors, either from the option assembly kit or sourced yourself. Assemble the PCB in the following order:

1. Install 1x2 and 1x3 pin headers: Vac/DC Trigger, 5/12V selection and Ser1. Carefully snap each one off the longer pinheader strip. Use tape (painter's tape works well) to hold them in place. Solder 1 pin and then verify the alignment. The header should be perpendicular to the board. If it is not, reheat the soldered pin and gently press it into place (watch the heat on the short headers!). Be sure to be gentle with heating headers as the plastic spacer softens quickly.
2. Install longer 1x headers : Spindle (1x4), I2C (1x6) and 5 Axis Headers (1x4). Use same technique as in 1).
3. Install 2X headers: TTL Relay Header (2x6) and Digital Input Header (2x3). Use same technique as in 1).
4. If you bought a Teensy 4.1 without headers, install pin headers. A solderless breadboard makes a great way to stabilize the pin headers while soldering the 0.1” header strips. (The photo below is just for illustration, that is not a Teensy.)

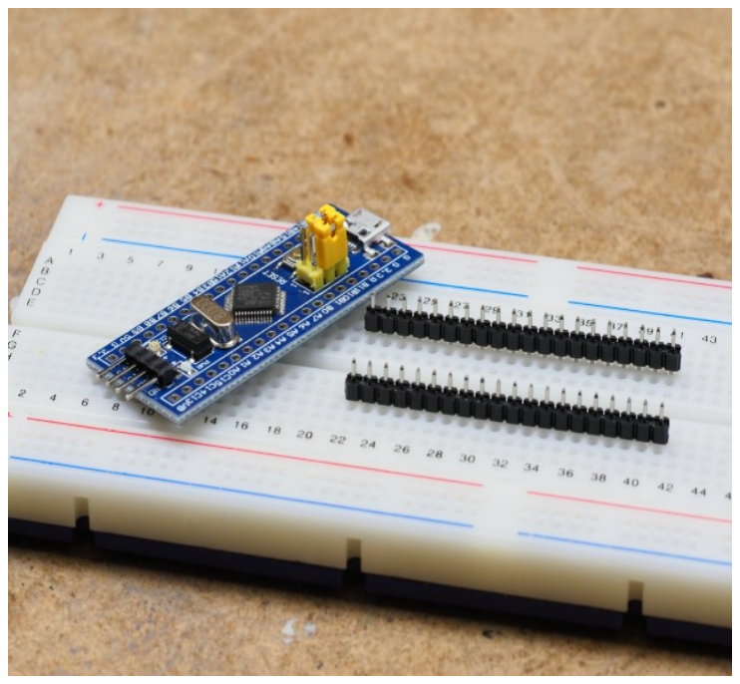
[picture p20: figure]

If using Ethernet, solder the 2x3 2 mm header in place on the bottom of the teensy 4.1. Use tape to hold it in place, solder 1 pin and check for alignment. If misaligned, reheat the soldered pin and press the header into correct alignment.

Then, solder the other pins.
5. Install R25. For V2.09 and earlier only. Skip this step if you have V2.10 or later. You can bend the leads to ensure it stays in place. But, also follow the the above approach of soldering 1 pin first, verifying alignment and then finishing. Note that a dual pinout footprint is used to allow several different types of trimmer potentiometer to be used. See BOM for more detail.
6. Install the Teensy 4.1. If using the sockets approach, place the sockets on the pin headers you just soldered onto the Teensy 4.1. Note, in the picture below, the 2x3mm pin header on the Teensy 4.1 is for testing purposes and not needed for the USB version. The Ethernet version uses a 2x3mm header that is attached to the underside of the Teensy.

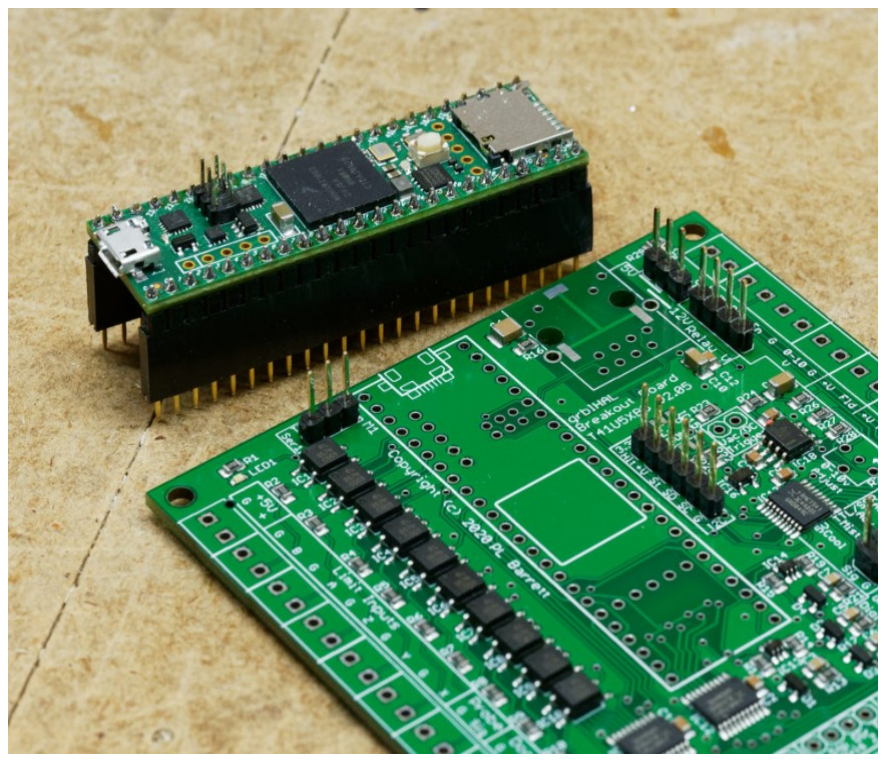
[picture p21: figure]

Now, gently inset the socketed Teensy 4.1 assembly into the indicated holes on the breakout board. Verify that all socket pins are correctly in place. Secure the entire assembly with tape on the component side of the board and then solder one pin on each of the different sockets and verify alignment. Once you are sure that the alignment is correct, solder the other pins, leaving the pins you initially soldered to last.
7. If using the direct solder approach, gently insert the Teensy 4.1 into the appropriate holes on the breakout board. Verify that all pins are correct and use tape on the component side to secure the Teensy 4.1 in place. Make sure the 2x3mm header for the Ethernet connection is properly inserted in the corresponding holes in the breakout board. Then solder 1 pin on each header, verify alignment and correct if necessary. Once satisfied with the alignment, solder the other pins, leaving the pins you initially soldered to last.
8. Mount and solder screw terminals. Assemble a complete row before soldering. The terminals lock together but are sometimes hard to get completely aligned. If that is the case, place them upside down (with the pins pointing up) on a hard surface and press each terminal in place with a screwdriver or similar. When you are satisfied that the tops are flush, insert and solder an end pin. Then solder the pin at the other end, making sure the row is properly aligned. It is sometimes helpful to solder the pin of middle a middle terminal while moving the row into proper alignment. Then solder remaining terminals while ensuring that the row is straight

Optional Components.

Many components are optional. Refer to the following diagram.
Notes:
- Ser1 and I2C headers are optional. grblHAL will work correctly without either header installed. Specific options may need them.
- EEPROM is optional, Install if you need to use an external EEPROM. grblHAL will work correctly without it.
- 0-10V Spindle control is optional. Use if you are using a VFD controlled spindle. grblHAL will work correctly without it if you are manually controller your spindle. We recommend installing the screw terminals as they are difficult to add later.
- Relays are optional. The T41E5XBB and T41U5XBB is capable of driving relay coils directly. It is recommended that you install the screw terminals even if you don't initially plan on using them. Installing later can be difficult. See note on Vacuum/Dust Collector relay below. But, grblHAL will work correctly without any relays.

- A and/or B Axes are optional if you don't have them in your CNC machine.
- Safety Door alarm. Install if you have an enclosure for your CNC machine with a Safety Door sensor. grblHAL will work correctly without it but you will need to load the a version of grblHAL with it disabled. Alternatively, you can simply put a jumper in the Door terminal.
- Axis pin headers. There are 5 sets of pin headers, one for each Axis. Install these only if you intend on using a them to connect to your stepper drivers. For reliability, screw terminals are recommended over pin headers. If using pin headers, we recommend using hot glue to secure the connector in place.
- Ethernet MagJack. If you are not using Ethernet, there is no need to install this. If using Ethernet, refer to the Setting up Ethernet section below.
- In general, we recommend that you install all screw terminals at the beginning. Adding them later can be difficult due to their interlocking nature.

### Relay Voltage

Relay Coil Voltage source is selectable between 5V and 12V (or higher) provided via an external power supply. Use a “suitcase jumper” as indicated on the PCB to select the desired voltage. One is provided in the basic assembly kit.

Note, we recommend you use an external 5V supply if you are driving 5V relay coils directly. To do so, you must disconnect the Teensy 4.1 +5V feed on the PCB. You will still need to power the Teensy 4.1 via the micro-USB connector. See Power Section for more information.

Relay coil voltage up to 24V is permissible and is applied at the input terminal labeled 12V. If using higher than 12V, we recommend changing resistor R29 to limit LED current to below 5 mA. For 24V, use 4.7K Ohm. The user is responsible for ensuring that all relays are rated for the voltage they provide.

Note: it is recommended to not use the stepper motor supply for the relay supply. It could be a source of EMI and cause erratic operation of the system.

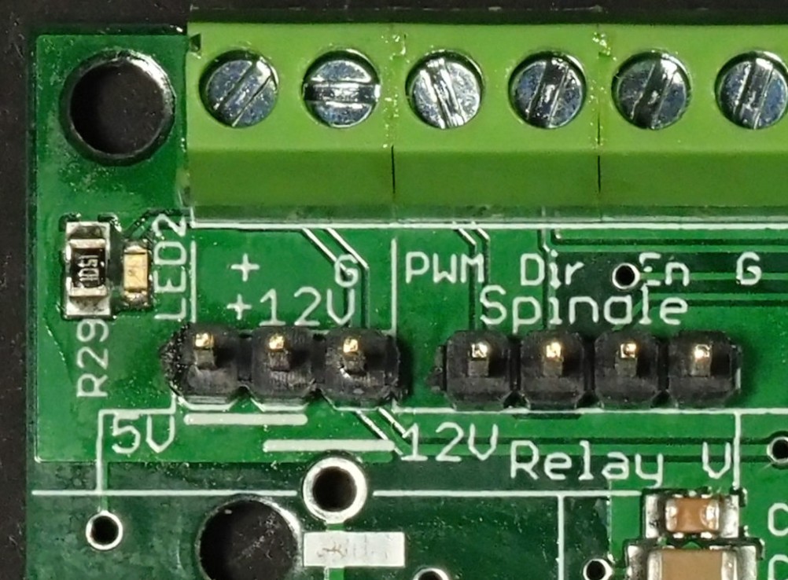
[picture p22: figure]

### DustCollector/Vacuum Control

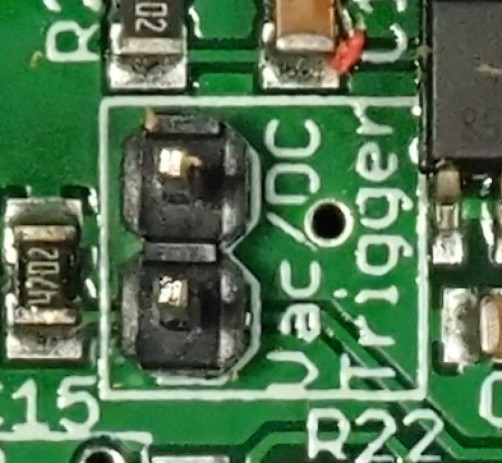
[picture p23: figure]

An additional driver is provided for a dust collector relay. It is activated whenever the spindle is turned on (M3). In addition, this relay output can be independently activated by a switch that connects to the pin header labeled Vac/DC Trigger. This makes it easy to do clean up with the same Vacuum or Dust Collector used for dust extraction while running your CNC machine. Automatic triggering of the Dust Collector can be disabled, see the PCB Level Configuration Section.

Building and Loading Firmware.

The grblHAL Web Builder is the primary tool for building firmware for the T41U5XBB. It is available at https://svn.io-engineering.com:8443/. (https://svn.io-engineering.com:8443/) Select iMXRT 1062 (Teensy 4.1) as the Driver and T41U5XBB as the Board. In the General panel, select the Number of axes. If you have a dual motor moving gantry, select that axis as Ganged or Auto-squared. If you have installed the Ethernet kit, In the Network/WebUI panel, select Ethernet and check Telnet server and WebSocket server options. Press Generate and Download Firmware button and save the file for loading. Be sure to save the configuration by clicking on the Save Board button. This will allow to you to later make changes without having to remember what you selected.

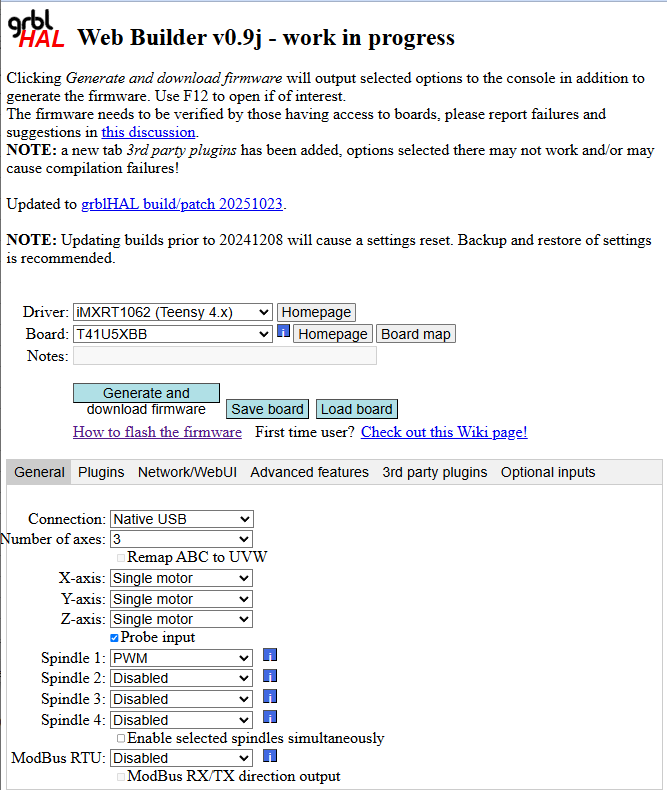
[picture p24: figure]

Spindle Sync

If you are building a CNC lathe and wish to use spindle sync, you will need to use a different board definition – T41U5XBB Spindle Sync. All other options are selected as suggested above. You will also need to make a board level configuration change to support this. See Spindle Sync in the PCB Level Configuration section below.

Loading Firmware

You will use the teensy.exe application available from pjrc.com. Start with this page - https://www.pjrc.com/teensy/loader.html and follow the links for you specific operating system.

Building from source code

In general, building grblHAL from source code is well beyond the scope of this document. You can download the source code at https://github.com/terjeio/grblHAL To build it, follow the instructions for Compiling GrblHAL in the grblHAL Wiki at https://github.com/terjeio/grblHAL/wiki/Compiling-GrblHAL. The grblHAL core Discussions section (https://github.com/grblHAL/core/discussions) is a good place to ask questions and get help.

### Running grblHAL on your machine

Once you have finished assembly, your grblHAL Teensy 4.1 based Motion Controller is ready to be tried out. Attach it to a PC via a USB cable and run a compatible GRBL sender application on the PC. We recommend ioSender and use it in our examples: https://github.com/terjeio/ioSender. Check for the most recent release. An overview of ioSender is available here: https://www.grbl.org/single-post/one-sender-to-rule-them-all.

Next, you will need to change the settings to reflect your hardware. Actual grbl setting values are also shown. Follow these steps:
1. Hook up your control buttons: Feed Hold, Cycle Start and Rest/EStop.
2. Open the Settings: Grbl panel. You will see a list of parameters that control grblHAL.
3. Set the “Invert Step Enable” mask. Check all boxes. $4=7 for a 3 Axis machine. $4=15 for a 4 Axis machine and $4=31 for a 5 Axis machine
4. Set “Invert Control Pin” mask. Invert Feed Hold, Cycle Start, Reset and Safety Door. $14 = 15.
5. Save these parameter and return to the main tab (Grbl panel, you should see the DRO section).
6. Press the Red Reset button if and ALARM state is showing.
7. Open the Jog panel and click on any of the job buttons. The DRO should show movement. If you have motors hooked up, they should show movement.
8. If you have any control buttons attached, test them. It should show activity. Note the associated “LED” in the G Code Sender application when you press a button. If nothing happens, you should verify your connections.
9. Close the Jog panel, fill in 1000 in the Spindle RPM box and click on the CW “radio” button. The LED on the Teensy should light up. Click on off and the LED should go off.
10. If everything works to your satisfaction, you should now proceed to full testing of your machine.

You can also refer to the grblHAL wiki's First Run Grbl Settings section: https://github.com/grblHAL/core/wiki/First-Run-Grbl-Settings (https://github.com/grblHAL/core/wiki/First-Run-Grbl-Settings)

Some Initial GRBL Settings

GRBL settings are dependent on your hardware so you might have to experiment a bit. Here are some key settings that will help you get going faster.

$ID | Name/meaning | Suggested Value | Comments
0 | Step Pulse time in uS | 5 | Default is 10 but 3 or 5 should work ok. Using the default may cause problems for step rates above 80 kHz.
4 | Step Enable bit mask, one per axis | 7, 15 or 31 | A 1 bit means invert. A 3 axis machine would have 7 as the value, a 4 axis machine would have 15, a 5 Axis - 31. Bit 0 is X, 1 is Y, 2 is Z, A is 3 and B is 4.
14 | Control pin inversion bit mask, one per pin. | 30 | A 1 bit means invert. Reset is bit 0, Feed Hold – 1, Cycle Start – 2, Safety Door – 3.
30 | Max spindle speed in RPM | 1000 or VFD max. | Default is 1000. If you have a VFD, you will need to set this to the spindle max. In G-Code, the Sxxx parameter controls speed and to get full speed, you will need have xxx match this parameter (S1000, in the case of the default).
100, 101, 102, 103, 104 | Steps/mm. One for each Axis. 100 – X, 101 – Y, and so on. | varies | Set these based on your hardware – lead screw, belt ratios, microstepping. The default is likely wrong for your machine but you will still get movement. On a per axis basis, determine the number of steps (including microsteps) it will take to make one full rotation of the lead screw. Determine how many mm that axis will move with one full rotation of the lead screw. Divide the first number by the second to get the value you will use.

Note, if you don't attach any switches, the system may come up in the alarm state before you change any settings. This is normal. If you are not using the Safety Door Alarm, in the Settings: Grbl tab, Invert control pins section, check the Safety Door box. This makes the system see the (nonexistant) Safety Door as closed. Similarly, you can invert the Halt. However, we highly recommended that you do not disable the Halt function and that you install a dedicated Halt button in a prominent location on your CNC machine.

You should spend some time studying all the GRBL settings. We suggest you start conservatively and tune your machine to higher performance one parameter at a time.

Compatible G-Code Senders

The vast majority of GCode Senders work with grblHAL. If your preferred sender is having problems, you may need to use a version of grblHAL built with compatibility settings. The grblHAL Web Builder allows you to select compatibility level when building firmware.

Setting up Ethernet.

If you wish to use Ethernet to connect to your breakout board, you will need to solder the network interface connector MAGJack in place. It is available in the Ethernet kit. See the BoM section for the part number if you don't want to buy the Ethernet kit. Once you have soldered it on the PCB, you will need to load a build of grblHAL that has been configured to use networking. You will use the USB connection to do that.

You will next need to load an Ethernet build of the firmware. Available via the grblHAL Web Builder (https://svn.io-engineering.com:8443/). (https://svn.io-engineering.com:8443/) Optionally, you can build a version from the source code at the grblHAL Github site.

To set up Ethernet, refer to this blog post for instructions: https://www.grbl.org/single-post/networking-the-t41u5xbb

Direct PC Connection via Ethernet

Many CNC users like to use a direct Ethernet connection between the PC and CNC machine. The advantage of this is the CNC machine is not visible from your network and is thus safe from intrusion and interference. Because grblHAL is not a secure system, this is the only way to network secure your CNC machine. Refer to this blog post for instructions: https://www.grbl.org/single-post/ethernet-without-routers-for-grblhal

Note that modern network switches prevent most interference and are quite inexpensive.

### 0-10V output setup

The 0-10V circuit works by using an opamp to filter a 5V PWM signal and amplify it to 10V. As such it needs 12V or higher input which the user must provide via the 12V screw terminals. A second order filter with an aggressive low pass cut off frequency is used to provide a stable signal for the spindle controller.

Because source voltage level can vary, the amplifier must be adjusted. You can do this by turning on your spindle in GCode (via Sxxxx) to full speed and adjusting R25 until the voltage on the 0-10V terminal reads 10V. Here is a step-by-step method you can use:
- Disconnect your spindle or VFD.
- In the Settings: Grbl tab, set $30, Maximum Spindle Speed, to 1000.
- Send the following command to grblHAL: M3 S1000. This turns on the spindle and causes the speed to be set to 100%. The LED on the Teensy 4.1 should light up.
- Measure the 0-10V output and G terminals.
- With a screwdriver, adjust the potentiometer labeled “0-10V Adjust” until the voltage is as close to 10V as you can get. Anything in the range 9.990V to 10.010V is acceptable.
- Send the following command to grblHAL: M5. This turns off the spindle.
- Reconnect your spindle or VFD and test.
- You may want to change the max spindle speed setting, $30, to something more appropriate for your machine.

You may want to repeat the above process with the spindle connected and running to fine tune the maximum speed.

### PCB Level Configuration

A number of features can be configured via solder jumpers on the bottom of the PCB.

Notes:
1. To help seeing any trace you need to cut, carefully scrape the green solder mask off the area between the pads. The trace should show up as bright copper. This will also make a solder bridge easier to create.
2. When you cut a trace, be sure to clean out and inspect the cut to ensure no stray slivers of copper are causing a short. Use a multimeter/DMM to verify the pads are no longer connected.

Spindle Sync

Spindle sync is supported in V2.20 and later versions of the T41U5XBB. This requires cutting 2 traces and solder jumpering two sets of pads. See the diagram below. Note, this changes the pin connections to the Teensy 4.1 and requires a special build of the firmware. See the Spindle Sync section in Building and Loading Firmware above.

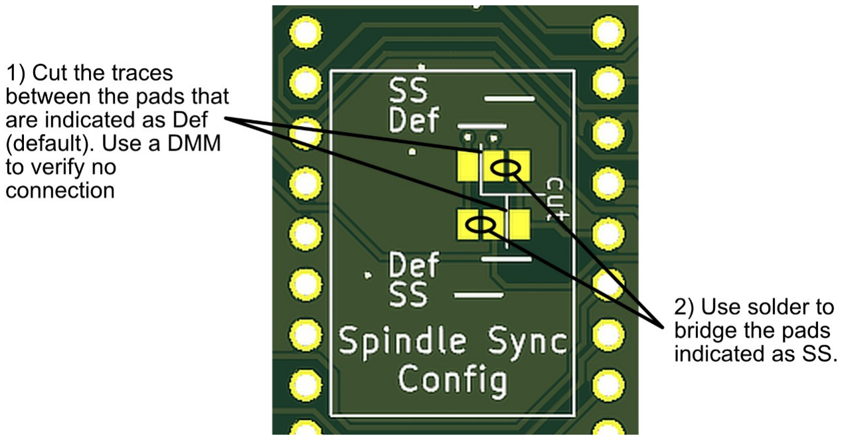
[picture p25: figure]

Individual Stepper Enables

No longer available as of V2.10.

By default, all 5 Axis Stepper enable signals are tied together. This is a common CNC machine configuration. If your machine needs separate enables for all or specific axes, you can configure this in the Axis Enable Configuration block on the bottom of the PCB.

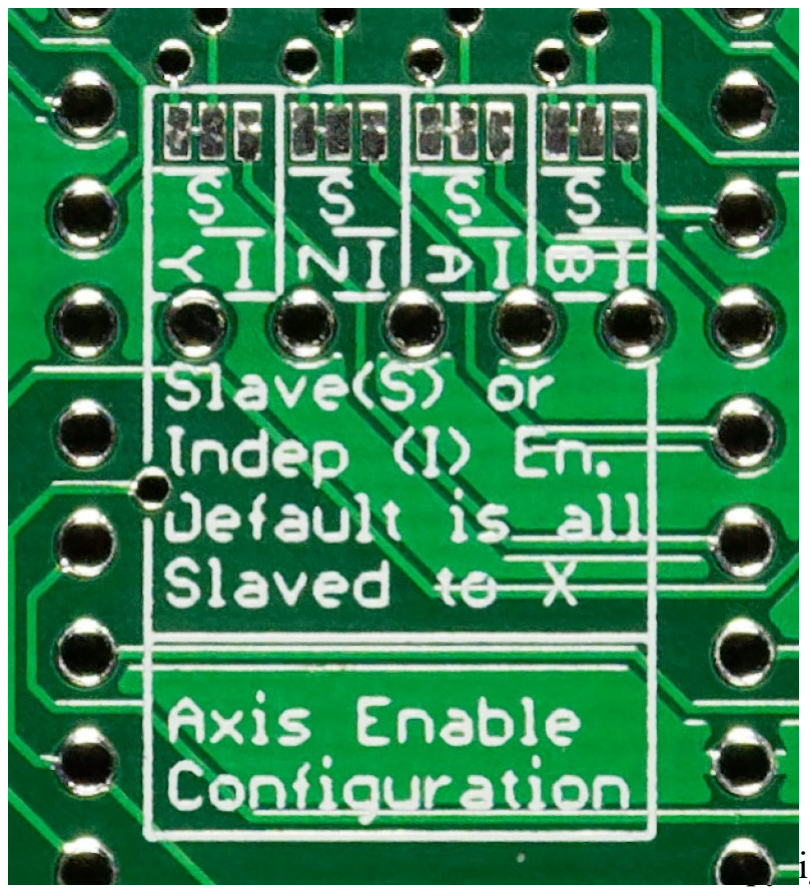
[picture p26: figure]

To make a given axis have an independent enable signal:
1. Locate the 2 way solder jumper associated with the axis you want to make independent. Note which side has the connection. It is marked with a horizontal line and an S.
2. Using a sharp knife, cut the trace between those two pads.
3. With a soldering iron, tin the center pad and the one one indicated with an I.
4. Then slowly add additional solder to the space between the I and center pads until there is a bead of solder that bridges between them.

If you wish to undo the configuration at a later date, use a soldering iron and wick to remove the solder bridge and then create a new one between the center and S pads.

External 5V Feed

The Teensy 4.1, when connected via USB, normally has enough power to support the 5V needs of the breakout board. You may wish to use external 5V in certain cases. We recommend you do this if using 5V relays. In that case, you will need to disconnect the base PCB from the Teensy 4.1's 5 volt supply. Note that there are 2 traces connecting the two pads. Disconnect 5V by cutting both traces between the pads in the external 5V block on the bottom of the PCB. Note that the Teensy will still need to be powered via USB.

Using a sharp knife carefully cut the two traces. Use the tip of the knife to ensure there is no connection. Test it for continuity with a multi-meter. When powered up via USB only (i.e. no additional 5V source used), the LED next to the +5V screw terminal should not light up. If it does, you need to repeat the above process. You will need to separately supply power to the Teensy 4.1, via USB from a computer or charger.

This process may be reversed by bridging the two pads with solder as described the above section.

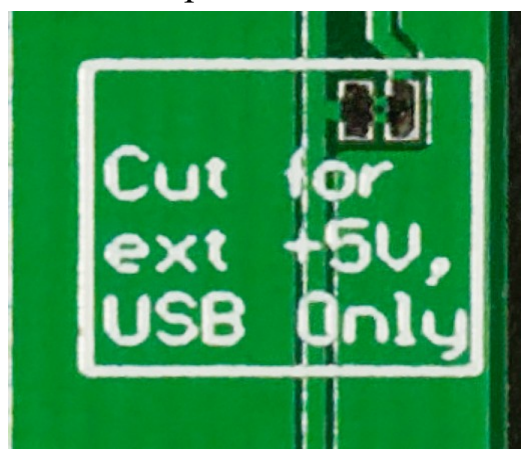
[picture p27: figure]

Vacuum/Dust Collector relay

No longer available as of V2.10.

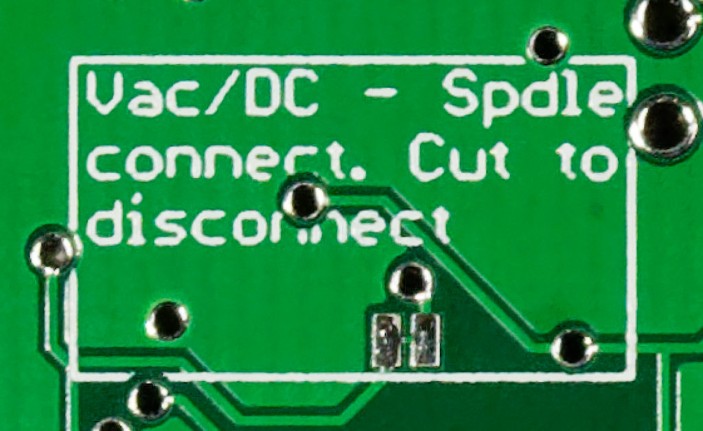
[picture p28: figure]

By default, the Vacuum/DC Relay is activated when the Spindle is enabled. You may disable this by cutting the trace between the two pads in the Vac/DC – Spindle Connect block on the bottom of the PCB.

This may be reversed by bridging the two pads with solder as described the above section.

Link A Axis to Y

No longer available as of V2.10.

This is for a dual motor Y axis configuration. The default configuration is A is not linked to
Y. When jumpered to Y, both Y and A axis motors will run in tandem, both getting the same signals. Using a sharp knife, carefully cut fully between the pads marked A (right two pads) and use solder to short the pads marked Y (left two pads). You should verify that there is no continuity between the two A axis pads as that can cause board damage.

Note that the traces to be cut may not be exactly centered in the pads.

This process may be reversed by bridging the two pads with solder as described the above section.

Note: this is not needed for current grblHAL and will not support Auto-Squaring. Configure Y as an Auto-squared Axis in the Web Builder.

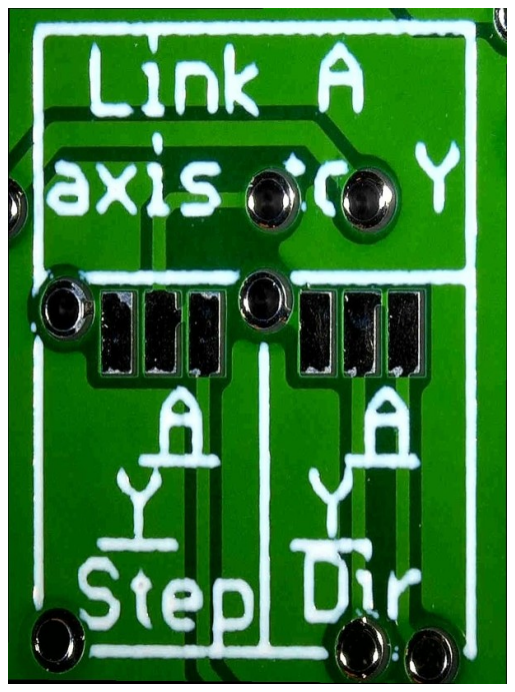
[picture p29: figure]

Relay Coil Voltage

No longer available as of V2.10.

Similar to the pin header selection of the relay coil voltage, you may configure the relay voltage via solder jumpers.

The default configuration has neither connected. Use the above solder jumper process to bridge the appropriate side of the two way jumper. You will need to short either the left pair of pins together for 12V or the right pair together for 5V.

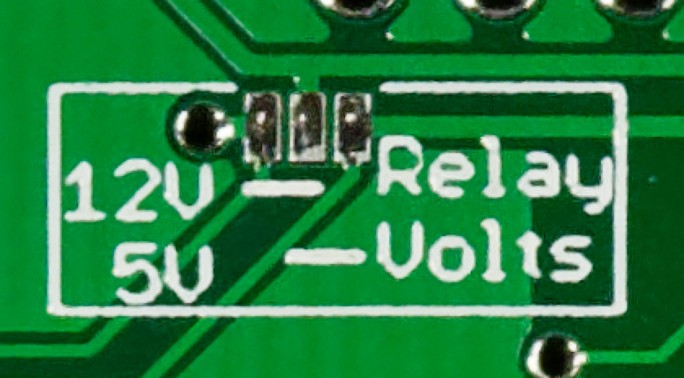
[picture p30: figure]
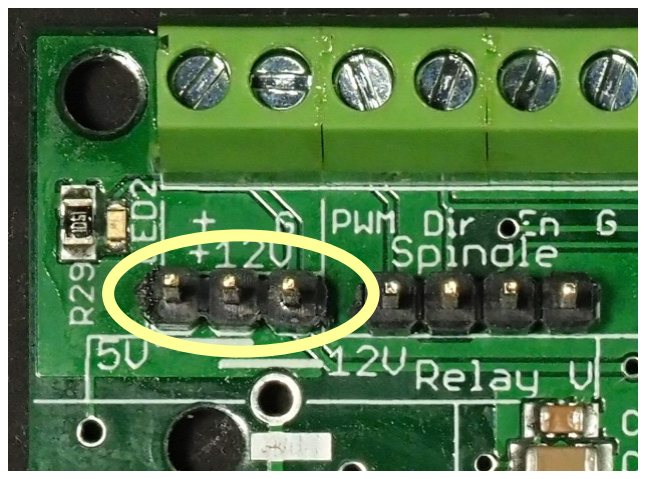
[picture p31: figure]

WARNING. If you do this, it is highly recommended that you remove (or not install) the pin headers from the relay voltage selection section to prevent accidentally routing 12V into the 5V sections of the board. Failure to follow this precaution will cause you to destroy your breakout board and the Teensy 4.1 by

inadvertently shorting 5V to 12V.

### Power and EMI Considerations

Clean, EMI-free power is important for smooth operation of the grblHAL motion controller system. In designing the T41E5XBB and T41U5XBB, we used good practices to avoid EMI but further precautions are recommended. Power is often a source of EMI and you should take additional steps to ensure that these sources are managed. Finding the source of interference later can be difficult – it is good practice to design your system with avoiding it in mind. General recommendations:
- Do not power 5V relay coils from the USB voltage supplied by the Teensy 4.1. Relays can produce EMI and power fluctuations. Use external power (see above).
- Do not power relay coils directly from the Stepper Motor power supply. It can be a significant source of EMI.
- Use shielded wires for signals. Makes sure the shields are grounded in a star configuration at the controller box or other common ground.
- Use ferrite filters on all wires entering or exiting the T41U5XBB or T41E5XBB PCB.
- Avoid routing wires near EMI sources such as a VFD, Stepper drivers, or power supplies. Avoid co-routing with wires that are connected to those devices as well.
- If you are connecting to the Teensy 4.1 via a USB cable, use one with a ferrite filter on it or add a clamp-on one close to the Teensy end of the cable.

If you are using Ethernet, and expect to not connect the Teensy 4.1 to a PC via USB, you will need to provide 5V for the Teensy. There are two ways to do this:
- Use a standard USB “charger” to power the Teensy 4.1 via the microUSB connector. We suggest a 1 Amp minimum capacity. This will work well if you aren't using 5V for relay coils.
- Provide 5V via the +5V screw terminal.

We recommend that all stranded wires have ferrules crimped on the end that goes into a screw terminal. This is a good practice in that it ensures the best possible contact and helps to avoid stray “cat whisker” strands of wire that could cause errors.

Using USB voltage for PWM control of VFDs

In some cases, the voltage supplied by USB may be lower than 5V. While the specification defines 4.75V as the minimum, some laptops computers USB ports output even lower voltage. This can cause lower than requested speeds when using the direct
PWM signal to control a VFD/Spindle. This does not effect the 0-10V output. This problem can be solved 2 ways:
1. By using external +5V to power the board. Remember to follow the instructions in the above “External 5V Feed” section.
2. By using the 0-10V output signal connected to the 0-10V input of the VFD. This requires you provide 12V to the board.

### Errata:

1. V2.05 digital inputs ST0-ST3 are not 5V tolerant. They will work correctly at 3.3V. This is corrected in V2.07.
2. V2.05 silk screen labels the Flood connection as Cool. This is corrected in V2.07.
3. V2.10 silk screen labels for Aux0, Aux1 and Aux2 are slightly misaligned. Corrected in V2.11.
4. V2.20 silk screen labels for Limit A and Limit B are incorrectly labeled Lim Z and Lim A, respectively. Corrected in V2.21.

### T41U5XBB Revision History

V2.05 Pre-Release version.
V2.07 Initial Version.
V2.09 Minor layout and silk screened label updates.
V2.10 Moved trimmer potentiometer from kit to base board. Update silk screened labels
V2.11 Silk screened label updates
V2.20 Upgraded opto-isolators. Minor layout changes. Improved mounting hole clearance. Added PCB level configuration of Spindle Sync. Silk screened text/label updates.
V2.21 Corrected Lim A and Lim B labels.

### Schematics:

Refer to the github repository for current versions schematics.

### Board and mounting hole dimensions

V2.07 – V2.09

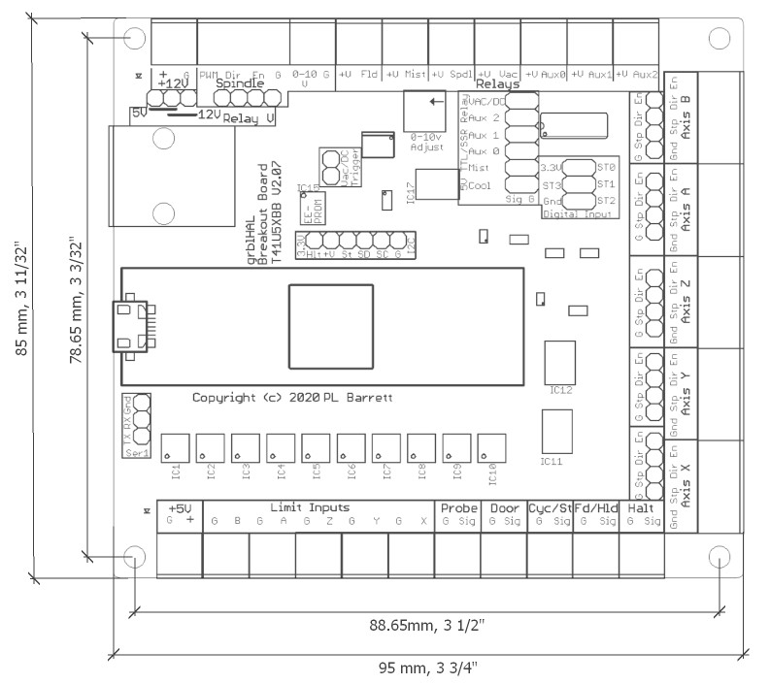
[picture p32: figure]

V2.10 and later.

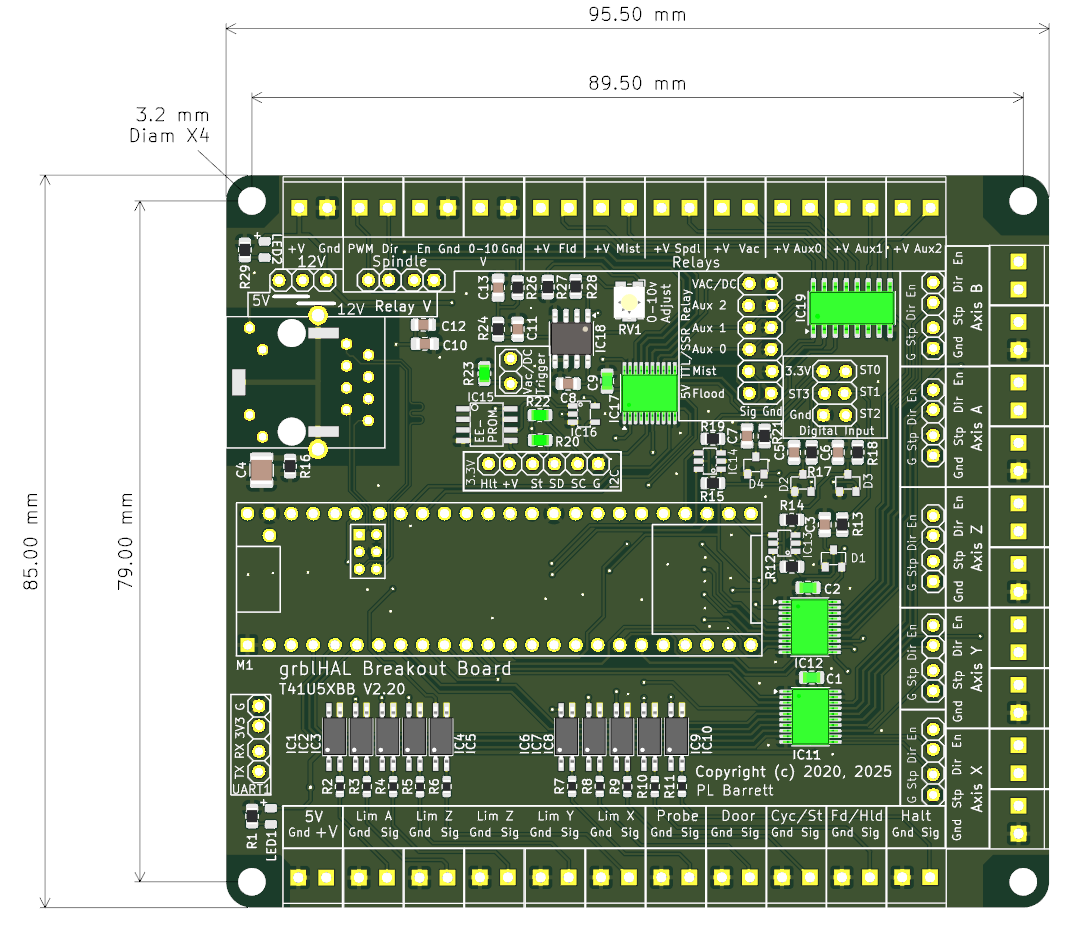
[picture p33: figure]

Bill of Materials for through hole components (for the “Unkit” version).

Item | Number | Source
2 pin 3.5 mm Screw terminal. | 32 | Readily available on ebay/amazon/aliexpress/...
1x2 2.54 mm pin header | 1 | Readily available on ebay/amazon/aliexpress/... Snap off of longer strips. [2]
1x3 2.54 mm pin header | 2 | Readily available on ebay/amazon/aliexpress/... Snap off of longer strips. [2]
1x4 2.54 mm pin header | 6 | Readily available on ebay/amazon/aliexpress/... Snap off of longer strips. [2]
1x6 2.54 mm pin header | 1 | Readily available on ebay/amazon/aliexpress/... Snap off of longer strips. [2]
2x3 2.54 mm pin header | 1 | Readily available on ebay/amazon/aliexpress/... Snap off of longer strips. [2]
2x6 2.54 mm pin header | 1 | Readily available on ebay/amazon/aliexpress/... Snap off of longer strips. [2]
1x24 2.54 mm pin header | 2 | For Teensy 4.1. If you purchase a Teensy with pins, omit these items. Readily available on ebay/amazon/aliexpress/... Snap off of longer strips. [2]
1x24 2.54 mm socket | 2 | Readily available on ebay/amazon/aliexpress/... [2][3] Higher Quality: Mouser – 801-87-024-10-001101, Digikey - 1212-1209-ND
Teensy 4.1 | 1 | Available from pjrc.com.
R25, 10K Potentiometer | 1 | Numerous sources. Mouser: 652-3362P-1-103LF, Digikey: 3362P-103LF-ND [1] [5]
T41E5XBB (Ethernet)
MagJack | 1 | Whiznet RB1-125BAG1A Mouser: 950-RB1-125BAG1A Digikey:1278-1011-ND
2x3 2 mm Header | 1 | Digikey:MTMM-103-10-T-D-355-ND, Mouser: 200-MTMM10310TD355 (drop ship from Samtec)[4]
2x3 2 mm Socket | 1 | Digikey: 17-2314820-6-ND, Mouser: 855-M22-7140342[4]

Notes:
1. The PCB has a dual footprint for the 10K trimmer potentiometer, R25. and will accept 2 different footprints: 3 pins in a row with 0.1”/2.54 mm pitch or a triangular layout with the middle pin offset by 2.54 mm. The first footprint is used by more expensive, higher quality multiturn trimmers and the second is very common and low cost. A multiturn trimmer will give a finer adjustment of the 0-10V output level. The BOM has the lower cost version. Also, you could use a 2K or 5K trimmer in place of the 10K one.
2. We recommend gold plated pin headers for reliability.
3. Single row sockets are also readily available from numerous sources though good quality ones are not that expensive. We recommend you use good quality, gold plated headers and sockets. Note: for using Ethernet with a socketed Teensy 4.1, care must be taken to select 2 mm and 2.54 mm headers and sockets that are similar in height. However, we recommend that you directly solder your Teensy 4.1 to the T41E5XBB PCB if using Ethernet.
4. Use if you decide to socket your Teensy 4.1. The 2 mm header and socket must be matched to the Teensy 4.1 socket and header height. If you solder your Teensy 4.1 in place, you will only need a 2x3 2 mm header but need to be sure it will be tall enough.
5. As of V2.10, this is included on the base board and is no longer part of the Through Hole BOM.

BOM for surface mount components.

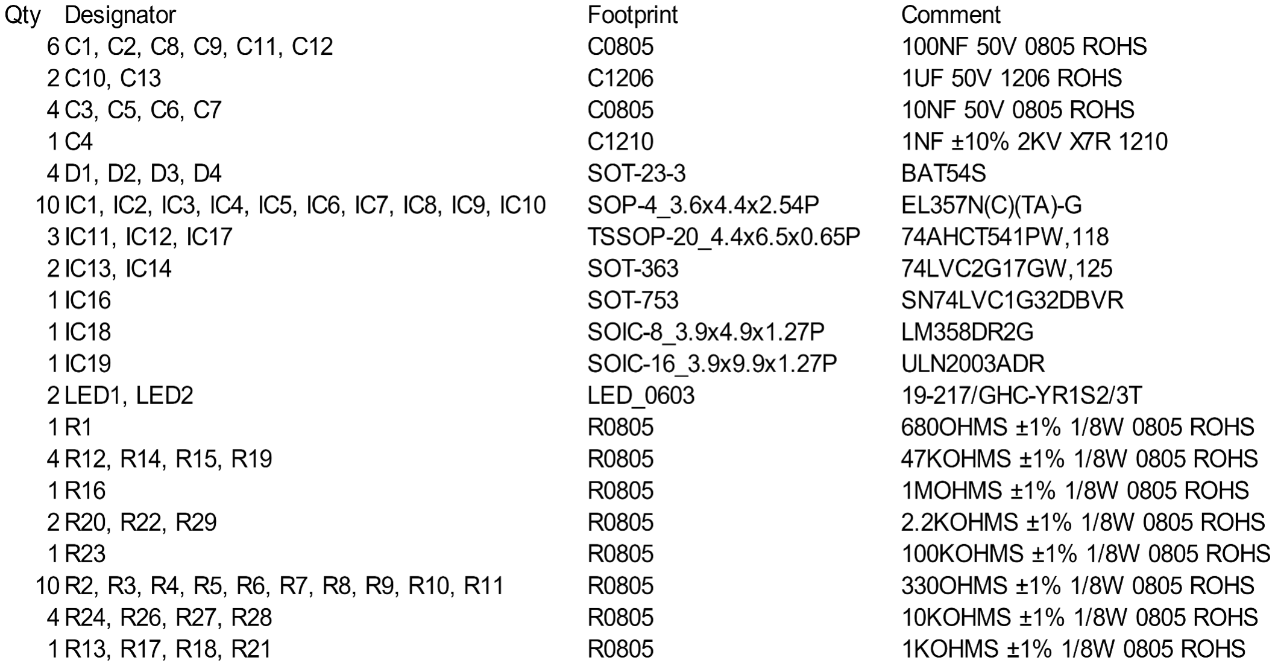
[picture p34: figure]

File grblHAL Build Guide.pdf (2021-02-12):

### Guide to building grblHAL versions for Teensy based systems

This document is depreciated in favor of the grblHAL WIKI section entitled “Compliing GrblHAL”, located here: https://github.com/terjeio/grblHAL/wiki/Compiling-GrblHAL

Though it may at first look complex, building grblHAL from source code is not hard. To build grblHAL for a Teensy 4.x, follow these steps:

1. Get Arduino. Download and install the Arduino development environment for your PC (https://www.arduino.cc/en/main/software). Consider donating, it is a worthy cause.
2. Get Teensyduino. Download and install Teensyduino (https://www.pjrc.com/teensy/teensyduino.html ).
3. Get the grblHAL code. Download the grblHAL zip file. (under Code on https://github.com/terjeio/grblHAL, select Download ZIP). Extract this directory structure to your development directory (on Windows it would be Documents/Arduino/). You should wind up with with a directory named grbl-HALmaster.
4. Configure grblHAL for the Teensy 4.x. Copy the grbl files to the IMXRT1062 directory. All files in grbl-HALmaster/grbl should be copied into grbl-HALmaster/drivers/IMXRT1062/main/src/grbl. Windows File Explorer users be careful to copy and not move (which is the default).
5. Build the Default Version. To build the default 3 Axis version: (You can skip this step if you want an enhanced version.)
1. Using the Arduino application File/Open to open the main.ino file in grbl-HALmaster/drivers/IMXRT1062/main.
2. In the Arduino application, go to Tools/Board/Teensyduino and select Teensy 4.1. (note earlier versions of Arduino just has a long list of boards to select from – find Teensy 4.1 on that list.)
3. Connect your Teensy 4.1 to your PC via a USB cable.
4. In the Arduino application, go to Tools/USB Type. It should say Serial, if not, select Serial.
5. In the Arduino application, go to Tools/Port. You should see an entry that says “ComXX Serial: Teensy 4.1”, select it.
6. Press the upload button in the upper left corner directly below the top menu bar. This will take a while as Arduino needs to compile a large number of files. Eventually the status bar at the bottom left of the screen should say “upload complete”.
7. Your board should be ready to test!
6. Using legacy G Code Senders. If you are getting odd behavior with your G Code Sender, you may need to set the compatibility level. This is common when using Java based or older G Coder Senders.
1. Open grbl-HALmaster/drivers/IMXRT1062/main/src/grbl/config.h. At about line 50 you will see
#define COMPATIBILITY_LEVEL 0

2. Change this to
#define COMPATIBILITY_LEVEL 10

3. Rebuild as in 5.6 and test. You could also try a level of 2.
7. Build an Enhanced Version. If you need 4 or 5 Axis support (or additional features), download configurations.zip (https://github.com/phil-barrett/grbl-teensy-4/blob/master/configurations.zip) and copy the relevent driver.c and driver.h files to the grbl-HALmaster/drivers/IMXRT1062/main directory and rebuild (Arduino app, Download button). The zip file contains prebuilt versions that you can just load into the Teensy 4.x – see Readme.txt in the .zip file for details. To change to a 4 or 5 Axis version you will also need to edit the config.h in the grbl-HALmaster/drivers/IMXRT1062/main/src/grbl directory. At approximately line 150, you will find:
// Number of axes supported: minimum 3, maximum 6
// If more than 3 axes are required a compliant driver must be provided
#define N_AXIS 3 // Number of axes

Change this to 4 or 5, depending on your machine setup, save the file and rebuild (Arduino app, Download button).

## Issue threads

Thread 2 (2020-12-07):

Laser raster speed

theomajigga, 2020-12-07:
Phil, great work on this. I know very little when it comes to this type of ports, but my realization of how cheap M4 boards have become, are leading me down the path to upgrade me co2 laser to a proper (freshly written) 32-bit port of GRBL.

First: Sorry for an issue report, I know this isn't the proper route.

Second: I am currently running GRBL-LPC for my laser, I get stuttering on high dpi, fast movements (254dpi/300mm/s). I am hoping to get some increased speeds out of my machine, as it is capable of 500mm/s (with out imploding :) )

Per Oz of the project Lightburn:

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

After doing extensive research, it led me to your project, and some of the work you did with the gnea fork.

I guess, my question is, would upgrading to the teensy 4.x and the board you have produced on tindie, get me the speeds I am looking for?

Thank you!

phil-barrett, 2020-12-07:
No problem posting in Issues.

I don't have solid answers for you but am pretty confident grblHAL on the Teensy 4.1 (600 MHz iMXRT1062 ARM M7) will outperform the LPC.

Some data - the old Grbl/gnea running on an ATMega 328P was limited to a step rate of about 30 kHz.  In my latest testing, I have seen step rates of up to 400 kHz on the T4.1/grblHAL.  I did a [blog about it here](https://www.grbl.org/single-post/how-fast-can-it-go). If the min step pulse width wasn't limited to 2 uS, I'm sure it could go faster.  Depending on the gearing and microstepping of your machine, you can get significantly higher speeds than 6000 mm/min (100 mm/s).

grblHAL allows building with a much larger input buffer and Terje's sender supports something called aggressive buffering which allows filling the input buffer so the communications link tends not to be the bottleneck.

You might also want to ask your question on the grblHAL issues list (they won't mind it at all). And, in fact Terje (Mr grblHAL) is very interested in laser support. He's looking at support PPI mode, for example.

theomajigga, 2020-12-16:
Awesome Phil, I wish my controller was more accessible. HAHA!

I think I will order one of your boards, not much I can break on my machine.

A couple notes:

1. Users that would move over to this system, will NEED to be able to use Lightburn, it is hands down the best piece of software. The aggressive buffering, I believe is used per comments in https://forum.lightburnsoftware.com/t/gcode-controller-transfer-mode/26006/14 I am willing to test this out, after the holiday season! Orders coming in ;)

Is there anything that I would be losing when moving over to this new board? I was reading through https://github.com/terjeio/grblHAL/tree/master/drivers and it seems that the GrblHAL operates the same(ish) on both the LPC1768 and the teensy. I guess, my question is, are there any lost features on GrblHAL vs the last GrblLPC (Just a port from Grbl 1.1f I believe), or will I at minimum gain features?

After reading through those drivers, I got more confused, but I believe that was stuff that Terje was just working on implement?

Thank you!

Cncninja, 2021-01-22:
Was there any resolve with laser use, I bought the new rev board but in the prebuilt firmware, i don't see a laser option also what board output would I use for my CO2 laser the PWM? or one of the I/Os? I would love to know how you connected yours up and the firmware used.

Thanks

phil-barrett, 2021-01-22:
I replied to your question on the grblHAL discussion section.  You should be good to go.

theomajigga, 2021-03-15:
Teensy is in, and Phil, your board should be arriving today, will be testing quite a bit with lightburn and the latest ""3 axis usb no opts" - 3 Axis, Aux Relays" release.

Hoping to have some good info and some deep testing in in the next few days.

theomajigga, 2021-03-17:
@Cncninja It is way faster, I used PWM of spindle and V+ (5V) two spots down. Using the increased planned buffer, running into a couple of issues that I am working on ironing out, but it works beautifully.

theomajigga, 2021-03-17:
TL is what my input is on my laser power source.

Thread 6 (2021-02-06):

YL620 and similar VFD spindles compatibility

garrett-rethink-contract, 2021-02-06:
Phil, have you personally tested the breakout board with a YL620 or other similar spindles by Huanyang. Or made by somebody...they don't really put a name on the device or the documentation.

The spindle accepts a 0-10V input, which they typically show being used with an external potentiometer wired between their 10V output, 0-10V input, and ground.

I find that when I try to control spindle speed this way, there is a nice big ground bounce that resets the Teensy.

I already had to isolate the EN and DIR outputs with external relays, because those inputs on the YL620 are NOT logic level, it wants to sink something like 15 volts through the FWD and REV inputs to XGND. However I'm a bit grumbly at the prospect of having to isolate the 0-10V output somehow, it's a bit more difficult of a problem.

Just wondering if you or anyone else ran into this and have some tips. Future PCB modifications might include an optoisolated section for the spindle; one could easily tie grounds together if they wanted, but the spindle enable, opamp, and opamp supply regulator could all live in an isolated island. PWM will go through isolation just fine.

macegr, 2021-02-06:
(ugh, sorry for the wrong account above. this is my usual account. I'm leaving it, and commenting here to make sure I see a response)

phil-barrett, 2021-02-06:
I have not tested it personally though I have several customers that use it as well as the PWM output with VFDs.

I have a new board coming that provides Isolated spindle (en, dir, pwm and 0-10V).  I was hoping to have it available in Feb but Chinese New Year and some additional debugging makes that wishful thinking.

I am open to resolving this situation how ever you would like. Return for a refund?  Credit for a future board?  Let me know.

macegr, 2021-02-06:
No chance on returning it, it's built into the machine and I'll use it in whatever way works, even if it's manual speed control :) The price on Tindie was suspiciously low, and I'd be excited to buy the upgraded version later whenever you release it.

phil-barrett, 2021-02-06:
OK.  If you do buy the next one, remind me of this conversation.

macegr, 2021-02-06:
If you want, you could go ahead close this issue since it'll be resolved with future hardware. I consider this to be completely acceptable since we're buying into sort of a bleeding edge system, this is the early adopter tax. I'm happy with the board overall and I still have start/stop/fwd/rev control as-is. Speed control on a router is a once per job type of adjustment.

phil-barrett, 2021-02-06:
Thinking about this last night, have you tried a toroid on the cable to the VFD?

macegr, 2021-02-06:
I tried series resistance, zener clamp, a ferrite bead. It didn’t help the situation. When the grounds aren’t tied together I can see a 120V waveform across them, but it’s weak (meter impedance too low but scope sees it). It occurs to me that the Pi, breakout, and its supply are not directly tied to chassis ground, will try that too.

macegr, 2021-02-10:
I can confirm that if you bond the Teensy ground directly to earth ground (green wire), and made sure the VFD, Teensy, breakout, computer (Pi in my case), and 24V power supply are all bonded together and to earth, the Teensy does not reset when the VFD 0-10V lines are connected and spindle is activated. I have speed control! The isolated version still sounds like a good idea since some motor spike is being dumped somewhere into earth, but it's working now.

phil-barrett, 2021-02-10:
Glad to hear it. VFDs and spindles are nasty devices from the electronics point of view.  Not as bad as HF Start Plasma Cutters, though.

Closed 2021-02-06.

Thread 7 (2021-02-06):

Issue in laser mode, laser turning on after movement, can't disable

TheAnt1dot3, 2021-02-06:
Hi,

I'm using your breakout board as both a cnc controller and sometimes switch to laser mode for etching.
The etching itself works fine, but i'm having issues with the laser constantly enabled or flashing.
for example, i have unplugged my usb and shut down external 5V power to my board. when i power it on and plug the usb in, the laser is flashing  (at full power it seems so it burns a hole in my board).
if i move in the positve X direction, the laser shuts off, but when i move in the negative X direction, it goes to full power and remains on until i move it to the positive direction again.

here are my config settings:
GrblHAL 1.1f ['$' for help]
client> $$
$0=10 (Step pulse time, microseconds)
$1=255 (Step idle delay, milliseconds)
$2=0 (Step pulse invert, mask)
$3=1 (Step direction invert, mask)
$4=7 (Invert step enable pin, boolean)
$5=0 (Invert limit pins, boolean)
$6=1 (Invert probe pin, boolean)
$10=510 (Status report options, mask)
$11=0.010 (Junction deviation, millimeters)
$12=0.002 (Arc tolerance, millimeters)
$13=0 (Report in inches, boolean)
$14=14
$15=0
$16=0
$17=0
$18=0
$19=0
$20=0 (Soft limits enable, boolean)
$21=0 (Hard limits enable, boolean)
$22=0 (Homing cycle enable, boolean)
$23=0 (Homing direction invert, mask)
$24=25.000 (Homing locate feed rate, mm/min)
$25=500.000 (Homing search seek rate, mm/min)
$26=250 (Homing switch debounce delay, milliseconds)
$27=1.000 (Homing switch pull-off distance, millimeters)
$28=0.100
$29=0
$30=1000. (Maximum spindle speed, RPM)
$31=0. (Minimum spindle speed, RPM)
$32=1 (Laser-mode enable, boolean)
$33=5000.000
$34=0.000
$35=0.000
$36=100.000
$37=0
$39=1
$40=0
$41=0
$42=2
$43=1
$44=0
$45=0
$46=0
$56=5.000
$57=100.000
$58=-5.000
$59=500.000
$60=0
$61=0
$62=0
$63=3
$64=0
$65=0
$100=6400.000 (X-axis travel resolution, step/mm)
$101=6400.000 (Y-axis travel resolution, step/mm)
$102=1607.000 (Z-axis travel resolution, step/mm)
$110=750.000 (X-axis maximum rate, mm/min)
$111=550.000 (Y-axis maximum rate, mm/min)
$112=600.000 (Z-axis maximum rate, mm/min)
$120=25.000 (X-axis acceleration, mm/sec^2)
$121=25.000 (Y-axis acceleration, mm/sec^2)
$122=200.000 (Z-axis acceleration, mm/sec^2)
$130=200.000 (X-axis maximum travel, millimeters)
$131=200.000 (Y-axis maximum travel, millimeters)
$132=200.000 (Z-axis maximum travel, millimeters)
ok
Below the commands being sent. X -100 triggers the laser to be on after about -20   X +100 seems to disable the laser around the same mark.

note that if the laser is in the negative X direction, i cannot disable the laser with M5S0 (if the laser is in the positive direction i can turn it off and on)

client> $X
ok
feeder> G91
ok
feeder> G0 Y10
feeder> G90
ok
ok
feeder> G91
ok
feeder> G0 Y10
feeder> G90
ok
ok
feeder> G91
ok
feeder> G0 Y10
feeder> G90
ok
ok
feeder> G91
ok
feeder> G0 X-100
feeder> G90
ok
ok
feeder> G91
ok
feeder> G0 X100
ok
feeder> G90
ok
feeder> G1F1
ok
feeder> M3S1000
ok
feeder> M5S0
ok
feeder> G91
ok
feeder> G0 X-100
feeder> G90
ok
ok
feeder> M5S0
ok
feeder> M5S0
ok
feeder> M5S0
ok
feeder> M5S0
ok
feeder> M5S0
ok
feeder> G91
ok
feeder> G0 X100
feeder> G90

the laser is wired to the +12v and G input and the signal is connected to the PWM port on the board.
i'm running around in circles trying to figure this out, so i'm reaching out for help here.

thanks,

Stef

phil-barrett, 2021-02-06:
First, off.  The PWM output is also use to drive the LED on the Teensy so you can disconnect your laser while testing this. The brightness of the LED is proportional to the S-parameter setting in GCode.

Sorry for the dumb questions.  I'm trying break this down a bit.

What grblHAL version are you using?  Did you build it yourself? What sender are you using?

Are you getting the laser powered on during rapid moves?  (G0)  Even following an M5?  By the way, M5S0 should be the same as M5 without the S-parameter.  M5 turns off Spindle/Laser PWM and Enable.

phil-barrett, 2021-02-06:
I am trying to reproduce the problem and am not seeing it.  I have a logic analyzer hooked up and any PWM output will get caught - nothing shows.

What is your laser HW and how is the board hooked up to it? Maybe some pictures of your wiring, if possible.

TheAnt1dot3, 2021-02-06:
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

No question is dumb :)  i'm running 1.1f  from the precompiled hex files you provided. nothing fancy on that side.
I will take some pictures of the wiring and upload them here. for the laser, i'm using one of those chinese '15 Watt' lasers, they have 3 pin connectors for 12v and pwm. this is the one i bought : https://www.wish.com/product/5e6472f81c32cb114b119e91?mi=3&share=web

Photos will follow soon :)

thanks for your help

TheAnt1dot3, 2021-02-06:
Here are the pictures as requested. 12v input has also the positive and negative (black & red) to the laser connected and PWM to the PWM port on the board.
https://ibb.co/GJg0W2L
https://ibb.co/92hG3wP

For sending the gcode i tried 2 programs both with the same problem. i tried lightburn and i tried cncjs.
I did note that, when enabled and disabling the laser as expected, the orange LED on the teensy is lit.
when i move my x-axis to the left (and the laser auto-enables) there is no orange LED lit on the teensy even though the laser is burning at full speed...

phil-barrett, 2021-02-06:
> when i move my x-axis to the left (and the laser auto-enables) there is no orange LED lit on the teensy even though the laser is burning at full speed...

OK, that means grblHAL and the Teensy aren't the ones turning on the laser. Do you have a multimeter?

Looking at the pictures, it is hard for me to tell how you have connected the laser to the breakout board. I see 7 wires and think this is the arrangement from left to right:
Flood - Black
V+ - Red and Green (2 wires)
G - Blue
PWM - Green
G - Black
+12V - Dark Grey (not sure color)

Where do each of those wires go?  And, I see a Yellow on the Laser connector, where is that connected?

Did the laser come with any hook up instructions? The web site didn't give much info.

TheAnt1dot3, 2021-02-06:
Unfortunatly no hook-up instructions...
Below some details on the wiring
Fld - Black    gnd to relay for controlling air
V+ - Red and Green (2 wires)   5v positive and signal wire to relay for controlling air
G - Blue   to black wire on laser - gnd
PWM - Green to yellow wire on laser - pwm
G - Black   gnd from external 12v power supply
+12V - Dark Grey (not sure color)   combination, 12 v input from power supply and also to red wire of laser for 12v positive

I do have a multimeter. Will post measurements from pwm tomorrow as it´s already past 11 pm here.

Thanks for thinking along

phil-barrett, 2021-02-06:
OK, talk to you in the morning.

A couple of things to try.  When the laser is firing and it shouldn't be, what is the voltage at the PWM output pin? Also, try disconnecting the relay for air (just the + wire).

TheAnt1dot3, 2021-02-07:
Sorry Phil, it seems the issue is not related to your fantastic board :) i have powered the laser directly to a 12v supply without pwm signal and i can measure the full 12v on the board of the laser.  If i disconnect the 3 wire cable i can only measure the positive and gnd on the cable.. it seems the faulty pwm comes from the laser controller board.. now i need to try and figure out where.. thanks for your help

phil-barrett, 2021-02-07:
I am happy to help with debugging this - if nothing else as someone to bounce ideas off of.  It helps me to provide better service and future products to my customers so I see a lot of benefit from it.

TheAnt1dot3, 2021-02-07:
That´s awesome Phil ! Thanks for that.
I just found out that, if i short pwm to ground it turns off..
Could it be, because i had the 12v input connected to the grbhal board input, where i also hooked up the 12v positive to the laser , and then i hooked the pwm and 12v negative to the spindle PWM ports ? Maybe i should try to connect the gnd  from the power supply directly to both laser and the spindle gnd port on the grbhal or wouldn´t that make a difference ?

TheAnt1dot3, 2021-02-18:
Hi Phil,

Because this issue was driving me crazy, i bought a brand new laser (completely different one [link ](https://www.amazon.de/-/en/gp/product/B087T7BB24/ref=ppx_yo_dt_b_asin_title_o00_s00?ie=UTF8&psc=1) ) but it is still not acting as it should. Got ground from separate 12V power supply hooked up to both the laser and the grblhal board,  PWM from grblhal to the pwm input for the laser and 12V positive from supply to the laser. as soon as i turn on the power supply, the Laser is getting fired and there is no way to turn it off. i measure about 4V on the pwm port even if the pwm should be disabled through commands (no LED lit on the controller) would it be worth a shot to try a pulldown resistor or something ?

phil-barrett, 2021-02-18:
Hmmm, if the LED on the Teensy is off, the voltage at the PWM terminal should be 0.  Try disconnecting it and see what it reads.  What does the enable terminal read when the LED is not lit.

Looking at that diode laser, it is possible it wants 12V PWM - the board provides 5V.  Not sure why it would read 4V, though.

TheAnt1dot3, 2021-02-18:
i've managed to get it working.. hurray :)
so, how i hooked it up was, the external 12v supply for the laser was wired directly to the laser and the ground was also hooked up to the grbl board. i connected the ground to the 12v input negative on the board. however, when i measured between that ground and the pwm pin, i kept getting about 3.6 volts no matter the pwm width.
if i measured between the pwn and one of the other ground pins, it was measuring as expected.
once i hooked the ground from the power supply to one of the other ground pins, it started working fine.

i'm guessing there is some separation between the 12v input ground and the rest of the grounds ?

TheAnt1dot3, 2021-02-18:
i will give the other laser another try tonight to see if it works..
and hide the results from my wife... otherwise i've wasted $200 lol

thanks again for your help Phil

phil-barrett, 2021-02-18:
Yeah, getting grounds sorted out can be a little tricky.  I like to think I'm pretty up on that stuff but still get surprised with floating values.

One can never have too many lasers...

Closed 2025-03-05.

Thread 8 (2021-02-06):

Component spacing

elfren, 2021-02-06:
While working on an enclosure design for the board I noticed the screw terminals spacing is not consistent.  Some are more than 3.5mm apart and some are less.  Also the upper left hole doesn't have enough space around it for an M3 SHCS.

Is the .brd file current or is this something which has been fixed in a later version?

phil-barrett, 2021-02-06:
The spacings aren't perfect. On the top row, the rightmost 8 2-pin screw terminals spacing varies between 6.987 and 7.03 mm. The bottom row varies between 6.95 and 7.05 mm. These are all well within the tolerances of the pins for the locking screw terminals. And, even a full row of screw terminals locked together is loose when inserted.  While not intentional, in future boards I will be deliberately varying pin spacings for connectors to tighten them up to make them stay in the holes when inserted. This makes soldering easier since they won't fall out when you turn the board over.

Yes, I am aware of the tight screw hole. It is still in V2.09. In future boards I will take more care of that.  For what it's worth. The 4-40 screws I use are fine.  That is no comfort to my European customers, though. I am now validating my designs with metric harware (as well as imperial).

elfren, 2021-02-06:
I just imported the .brd file into Fusion 260, then imported the M3 SHCS from McMaster-Carr.
If I understand you correctly, you're going to change the pin spacing in the connectors components to be less than or greater than 3.5mm, but the center to center spacing between components will be the spec distance.  That sounds like a good plan.

Thanks.

phil-barrett, 2021-02-06:
Yes.  Definitely for 4 pin connectors.  Still deciding for 2 pin ones. I've made a couple of test boards and it seems ok. This is especially nice for pin headers that not only fall out but are hard to get perfectly straight.  I plan on making fully assembled boards available and am worrying about DfM (Designing for Manufacturability). I want all the headers and terminals perfectly straight. One thing that really bothers me is when I buy a board and find wildly misaligned connectors.  Says the manufacturer doesn't care.

Closed 2021-02-06.

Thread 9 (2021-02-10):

Compiling help

Cncninja, 2021-02-10:
I've been fighting with this for a few weeks, and wonder if you could just make a precompiled version of the 3axis for lasers. I need the buffer changed to 1024 so I can move faster I have a 60W laser so I can move a bit faster than the LED lasers. Ive tried everything to compile, Ive used your guide but ran into the same thing as others with different/missing folders. I tried compiling using the most current Grblhal build and instructions and get an error ( no IOport.h file) but can't find where or what is even calling for it.  I just need a 3 axis with homing switches (No Z tho) and the buffer set to 1024 and the 30k step limit removed.

Thanks

Cncninja, 2021-02-10:
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

phil-barrett, 2021-02-10:
Here you go.  [3, 4 and 5 axis with planning buffer set to 1024](https://github.com/phil-barrett/grblHAL-teensy-4.x/blob/master/grblHAL_pb1024.zip). 30K limit does not exist in grblHAL.

Cncninja, 2021-02-10:
Thanks, I really appreciate it, any idea about the ioports.h error i would really like to understand why its not working for me, also if grblhal does not have step rate limits why is it still defined in the config file

// Sets the maximum step rate allowed to be written as a Grbl setting. This option enables an error
// check in the settings module to prevent settings values that will exceed this limitation. The maximum
// step rate is strictly limited by the CPU speed and will change if something other than an AVR running
// at 16MHz is used.
// NOTE: For now disabled, will enable if flash space permits.
#define MAX_STEP_RATE_HZ 30000 // Hz

phil-barrett, 2021-02-10:
OK, forgot about that.  Never had that enabled for any of my builds.

I'm not sure why you are seeing the ioports error.  could be a mix and match thing. I built with the master branch and keep it pure.  If you download the test over the master branch (or the other way around) you might wind up with left over files. The arduino IDE by default will try to compile everything.

Cncninja, 2021-02-11:
Worked like a charm !!! the laser is up and running.

phil-barrett, 2025-03-05:
To bring this forward, the grblHAL Web Builder will allow people to build their own firmware without needing to compile.

Closed 2025-03-05.

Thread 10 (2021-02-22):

Npn or pnp 3 wire inductive sensors

raenji-sk, 2021-02-22:
Hi, does the breakout board support the inductive sensors? I am currently running some 6-30V PNP NC ones with my current arduino setup and would like to continue using them as I find them very reliable. I see you have some boards in stock on tindie and want to get one, but this is something I have not found in your documentation and I am not sure they are supported. Can they be powered by an external PSU and plugged in your board. You say the inputs are optoisolated, so I think it should be fine, can you please confirm this? Also are all 5 endstop inputs isolated?

phil-barrett, 2021-02-22:
I am using inductive sensors on one mill but am running them at 5V,  They were listed as 6-24V.

All 5 limits go through optoisolators but share a common ground with the processor.  If your sensors are open collector then they should work. If they are "Push-Pull" or sourcing (as opposed to sinking), then not as it will feed high voltage back into the power supply.

I am putting the finishing touches on a Pro version of the breakout board that has truly isolated inputs and spindle. Optos runs off 12V. Pluggable screw terminals,  Maybe ships in a month.

raenji-sk, 2021-02-22:
Alright, thanks for the reply. I'll have to double check on that, in worst case I'll get some new sensors, mine do not work at 5V for sure, I run them at 12V at the moment. I did make the purchase in the meantime so I'll have to figure it now anyway 😉. The grbl HAL and  your board has been on my mind for a long time. I really like it does not use the step sticks and rather than that it has outputs for external drivers among other things. I'll be checking for updates regarding the pro version for sure and eventually get it later on after getting a bit familiar with this one and seeing how it performs compared to the Arduino GRBL. I guess you can never have enough hardware handy for any possible new projects.

phil-barrett, 2021-02-22:
>
> I guess you can never have enough hardware

Truer words were never spoken!

I do lose a lot of sales to step stick boards.  I just can't imagine using
them to drive a spindle through anything.

That said, I will probably release a board supporting them - mainly for
small laser machines.  The new TMC5160 is a very capable stepper driver and
can handle a lot higher current.  Too bad those pin headers do not.

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

raenji-sk, 2021-02-23:
> Too bad those pin headers do not.

That is a very good point.

raenji-sk, 2021-03-25:
Got the board up and running. Inductive endstops work without issues. Just had to solder some 1k8 resistors between signal and ground so they get pulled to zero. Will do some test cuts tomorrow.

raenji-sk, 2021-03-26:
Everything works great using bCNC as GCode sender. Closing Issue.

sogeniusio, 2023-02-15:
> Got the board up and running. Inductive endstops work without issues. Just had to solder some 1k8 resistors between signal and ground so they get pulled to zero. Will do some test cuts tomorrow.

Is this the official method for getting an inductive probe to work with the grblHAL probe? How reliable is soldering those 1k8 resistors?

Closed 2021-03-26.

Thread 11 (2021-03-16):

Can't set PWM pin inverse (Active Low) Gives error about homing cycle

theomajigga, 2021-03-16:

theomajigga, 2021-03-16:
Hooked pins up to PWM and 5V+ and fixes that issue.

Closed 2021-03-16.

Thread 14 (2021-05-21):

Aux Relay Outputs?

mlewus, 2021-05-21:
Does anyone know if there is any standard mapping for the use of the Aux 0, 1, & 2 relay outputs in GRBL on the breakout board?

raenji-sk, 2021-06-07:
http://linuxcnc.org/docs/html/gcode/m-code.html#mcode:m62-m65
I use theese to control one of the aux pins. Had to modify the postprocessor for fusion 360 so that it triggers it. I use it to turn on/off the vacuum independently of the spindle.

ericspooner, 2022-07-12:
For anyone finding this, I found based on the above:

M64 P0 = Aux 0
M65 P0 =Aux 0 off

M64 P1 = Aux 1
M65 P1 =Aux 1 off

M64 P2 = Aux 2
M65 P2 =Aux 2 off

I'm guessing M62PX and M63 PX Spindle On/Off and Vac On/Off, but I didn't get +5V out of them, though I haven't spent much time with the board yet.

phil-barrett, 2022-07-12:
Spindle and (and Vac) are controlled by M3 (on, forward), M4 (on, reverse) and M5 (off).

FWIW, M7 turns Mist on, M8 turns Flood on and M9 turns them both off.

The LinuxCNC GCode manual describes the M62-M65 behavior. [Relevant section](http://linuxcnc.org/docs/html/gcode/m-code.html#mcode:m62-m65).

ericspooner, 2022-07-12:
Thanks for the response! I got my board this weekend, and I did notice those turned on, but wasn't sure if you could separate them to use the M62's or not. Looking forward to more testing with the board!

cuishuang413, 2024-01-19:
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

Hello everyone, I tried M64 and M65, it doesn't look like it's doing anything. I'm using a custom grblHAL firmware, is there some config I need to define to enable it?

Thanks,

phil-barrett, 2024-01-20:
Where are you testing the voltage?  At the screw terminals or the pin headers?

The screw terminals are open collector outputs so will not show a voltage.  These essentially act like a switch.  [This](https://www.grbl.org/single-post/using-relays-with-grblhal-and-the-t41u5xbb) describes it in more detail. By the way, you need to jumper the relay voltage selection header, as well.

For more info on using the open collector screw terminals, [check here](https://www.grbl.org/single-post/ttl-ssr-on-the-screw-terminals).

cuishuang413, 2024-01-20:
I was testing them on the pin headers. And it turns out that I didn't have the correct board selected. Thanks anyways!

Perlovka, 2025-01-13:
>The screw terminals are open collector outputs so will not show a voltage. These essentially act like a switch.
>By the way, you need to jumper the relay voltage selection header

These two sentences are mutually exclusive, aren't they?
I've set jumper to 12v, issued M3 S6000 and spindle relay is showing 12v on screw terminals.
So this can not act like a simple switch, isn't it?

On my inverter there is X1 output 12v that should be pulled to GND to run spindle. But there is no option on the board for such a function as far as I understand from documentation.

phil-barrett, 2025-01-13:
It does act like a switch but not between the two relay coil terminals.  The relay coil drivers are open collector outputs.  The +V pin is connected to the relay voltage selected by the 3 pin header. The signal output is connected to the collector of a darlington transistor.  When the transistor is turned on (signal output high) it "connects" the collector pin (the one not labeled +V) to ground.  The relay coil needs to be connected the +V pin and that pin.  Current will flow through the relay coil when the output signal turns on the transistor. Hopefully, this diagram will help.

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

stevempotter, 2025-01-14:
When designing your boards, why didn't you use an FET to switch relay coils rather than a Darlington pair of transistors?

phil-barrett, 2025-01-14:
A MOSFET has advantages over a bipolar darlington pair but there are additional components needed for either - resistors to limit base (or gate) current, a pull down to prevent glitches on startup and a diode to protect the transistor(s) from back EMF. The ULN2003 has all that in a single package for 7 outputs. A MOSFET could handle higher current but for the purpose of driving relay (and perhaps solenoid) coils, the ULN2003 is a reasonable and cost effective choice.

stevempotter, 2025-01-14:
Thanks for that great comparison of MOSFETS vs Darlingtons, and explanation of your design choices!

phil-barrett, 2025-01-14:
No problem.  One other thing about bipolar transistors is they are pretty rugged which I think is important for this application. It doesn't hurt that they are fairly cheap.

BTW, there is a mosfet version of the ULN2003 that should drop in without modification. However it is several times more expensive (probably due to significantly lower production volume). Given this is a low cost product, I am hesitant to add cost without a very clear benefit.

Closed 2025-03-05.

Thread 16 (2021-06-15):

Setting up teensy 4.1 for first time run using bCNC

krupis, 2021-06-15:
Hello. I have purchased development board and teensy 4.1 I would like to know how to get it running for a simple test.

I have flashed the device with the simple 3axis compat hex file.

Is it possible to connect teensy 4.1 microcontroller to the PC and run the bCNC software to change some configurations? After I try to make a connection, I get an alarm state as been discussed multiple times already, and it does not allow me to call $HELP in terminal - it does not return anything. How to overcome this issue?

Do I must connect teensy to development board and short all button inputs to prevent the alarm from happening? Is there anything else I need to do?

For my application, I only use HALT, STOP and Cycle Start buttons. The other 2 ( Probe and Door) are not used. Since they are NC, do I must short them together to prevent them from causing fake alarms?  Thanks in advance hoping to hear back soon.

phil-barrett, 2021-06-15:
OK. Check out the [First Run Grbl Settings](https://github.com/terjeio/grblHAL/wiki/First-Run-Grbl-Settings) in the wiki.

You can temporarily short Halt to ground.  Then go in and change Grbl Setting ($14) to invert EStop. You might need to use MDI to do a soft reset ($X).

I recommend you move to a more recent build.  The [ethernet builds](https://github.com/phil-barrett/grblHAL-teensy-4.x/blob/master/ethernet_configurations.zip) will work ok without ethernet and are more current. The Grbl Setting interface will change to a much more human usable form, worth it for that alone.

bCNC and grblHAL work fine together but make sure you have a recent one as older versions had issues. If you are running it on Linux (or RaspPi OS) make sure you have the correct tty selected (it's a common mistake).

Closed 2025-03-05.

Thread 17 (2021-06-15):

$help command does not return the list of settings

krupis, 2021-06-15:
Hello. I have previously used the grblhal firmware on the esp32 device. I was able to write $help in terminal and it would respond with all the possible settings. For example $help limits would return:
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

Is there such possibility with teensy 4.1 grblhal? I have flashed the teensy with 3axis compat firmware but $help does not return setting list.

phil-barrett, 2021-06-15:
Switch to the newer builds I mentioned - you will see this:
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

krupis, 2021-06-17:
Hello. Thanks for the response. I have flashed the device with the ethernet configuration. Typing $Help in terminal still does not show the menu that you have provided. Can you explain how to invoke this help arguments menu? Also, could you please send me which documentation I should refer to when using grblhal?  Simply googling "grblhal command list" returns this one :
https://github.com/terjeio/grblHAL/blob/master/doc/markdown/settings.md

But if I understand correctly, this is not the latest documentation, please can you confirm which one should I use?

phil-barrett, 2021-06-17:
What build of the firmware did you flash? Which sender are you using?

krupis, 2021-06-17:
Im using the first build ( 3 axis with enc) and using bCNC

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

phil-barrett, 2021-06-17:
Ah, you need to move to a later build (Feb 2021 trimeframe or later).  You can use the ethernet builds I put up.  USB works fine with them. [Look here](https://github.com/phil-barrett/grblHAL-teensy-4.x/blob/master/prebuilt.md) and scroll down to the ethernet build section

krupis, 2021-06-17:
Okay tommorow I wil try to flash download configuration from your link and
flash with 3 axis quad enc ethernet build

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

krupis, 2021-06-18:
Hello. I have downloaded the ethernet_configurations folder from the link you have provided : https://github.com/phil-barrett/grblHAL-teensy-4.x/blob/master/ethernet_configurations.zip . I have flashed the teensy with the 3 axis with quad enc. The behaviour is exactly the same, I do not get any information display when typing $help. Please can you assist me further to find a cause to this?

After connecting and typing $help:
'''
ok

ok
$#
[G54:0.000,0.000,0.000]
[G55:0.000,0.000,0.000]
[G56:0.000,0.000,0.000]
[G57:0.000,0.000,0.000]
[G58:0.000,0.000,0.000]
[G59:0.000,0.000,0.000]
[G59.1:0.000,0.000,0.000]
[G59.2:0.000,0.000,0.000]
[G59.3:0.000,0.000,0.000]
[G28:0.000,0.000,0.000]
[G30:0.000,0.000,0.000]
[G59.6:0.000,0.000,0.000]
[G92:0.000,0.000,0.000]
[TLO:0.000,0.000,0.000]
[PRB:0.000,0.000,0.000:0]
ok
$G
[GC:G0 G54 G17 G21 G90 G94 G49 G98 G50 M5 M9 T0 F0 S0.]
ok
$help
error:5
$#
[G54:0.000,0.000,0.000]
[G55:0.000,0.000,0.000]
[G56:0.000,0.000,0.000]
[G57:0.000,0.000,0.000]
[G58:0.000,0.000,0.000]
[G59:0.000,0.000,0.000]
[G59.1:0.000,0.000,0.000]
[G59.2:0.000,0.000,0.000]
[G59.3:0.000,0.000,0.000]
[G28:0.000,0.000,0.000]
[G30:0.000,0.000,0.000]
[G59.6:0.000,0.000,0.000]
[G92:0.000,0.000,0.000]
[TLO:0.000,0.000,0.000]
[PRB:0.000,0.000,0.000:0]
ok
$G
[GC:G0 G54 G17 G21 G90 G94 G49 G98 G50 M5 M9 T0 F0 S0.]
ok
'''

I can see that the HEX file I have used for flashing was last modified January 29. Would this be the correct HEX?

phil-barrett, 2021-06-18:
What does $i report?

krupis, 2021-06-18:
```
$i
[VER:1.1f(IMXRT1062).20201103:]
[OPT:VNMSL,35,1024,3,0]
[NEWOPT:*FLASH,ES,ETH,TC]
[DRIVER VERSION:201014]
[DRIVER OPTIONS:USB.2]
[BOARD:T41U5XBB]
[IP:0.0.0.0]
[PLUGIN:ENCODER v0.01]
ok
b'$G\n'
[GC:G0 G54 G17 G21 G90 G94 G49 G98 G50 M5 M9 T0 F0 S0.]
ok
```

phil-barrett, 2021-06-18:
Ah, just checked the binary.  I'm sorry, needs to be newer. Use this.  I will update the zip file in a bit.
[3 axis eth.zip](https://github.com/phil-barrett/grblHAL-teensy-4.x/files/6674612/3.axis.eth.zip)

krupis, 2021-06-18:
Yes! Works as expected now. Surprised no one has noticed that before :o

Closed 2025-03-05.

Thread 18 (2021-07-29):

RJ45 MagJack

karoria, 2021-07-29:
Hi @phil-barrett
I am curious about what "magjack" really is, and is it compulsory requirement for ethernet connection on teensy4.1? I am designing my custom PCB for grblHAL. Can I use regular shielded RJ45 pcb connectors?
I plan to use RJ45 mounted on PCB with tracks instead of using that popular kit with flat cable.

phil-barrett, 2021-07-29:
Ethernet requires a very specific set of transformers, "magnetics", to work.  In the early days of twisted pair ethernet they were separate but most ethernet products use the version that is integrated into the RJ45 jack - thus MagJack - short for magnetic jack.

You can use any 100BT magjack but you will need to make the correct connections - they are all different. Unfortunately, the datasheets tend to not give much detail about how to connect. Probably your best bet is to use the PJRC magjack kit as the basis for your design.

Here are 2 docs that can help you dig deeper. Unfortunately, the info is buried in the middle of them
https://www.ti.com/lit/an/snla079d/snla079d.pdf?ts=1591489614886&ref_url=https://www.google.com/
https://www.analog.com/media/en/technical-documentation/application-notes/EE-269.pdf

karoria, 2021-07-29:
@phil-barrett, that is completely new to me. Till now I was understanding that all RJ45 are same and doesn't have any circuitary inside it. Thanks for pointing me to right direction and reading material. I will manage from it. Thanks again for your time.
Regards,
Ravi

Closed 2021-08-11.

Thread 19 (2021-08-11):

Compiling with Backlash compensation Enabled

humneraudio, 2021-08-11:
Hi,

I've been using the breakout board with Ethernet and bCNC - its running very well. I currently run it on Linux with a dedicated NIC to the teensy breakout board. I used the prebuilt firmware "3 axis eth quad enc.hex"

If I trigger $$ it doesn't return any $160/$161/$162 values, so I assume backlash compensation isn't enabled in this firmware build. Is that correct?

I want to try backlash compensation - however I feel its a little out of my depth in compiling a custom firmware that matches the 3 axis eth quad enc.hex firmware and includes backlash compensation. As everything already running so well, I'm concerned there maybe some specific options enabled which I might miss if I were to compile something myself.

I need some guidance, or if someone can build me the hex that matches the "3 axis eth quad enc.hex" + backlash compensation, that would be great.

phil-barrett, 2021-08-11:
You are lucky!  I am heading to airport in an hour and will be gone for a month.  Here is a hex that supports backlash. There seems to be a problem with the encoder plugin and I don't have time to track it down.  Hope it is not vital to you.

Also, could you post details of how you got ethernet working with bCNC on the RasPi?

[3X_eth_backlash.zip](https://github.com/phil-barrett/grblHAL-teensy-4.x/files/6969828/3X_eth_backlash.zip)

humneraudio, 2021-08-11:
Hi Phil,

Thanks! I will give this a go later today.

Regarding Ethernet on bCNC -

My CNC is a fixed gantry 3 axis machine - the only additional auxirlary components wired in are are NC Limit switches and NO eStop, RUN and HOLD buttons. I have homing enabled with soft limits.

I'm running latest Lunbuntu with the latest bCNC install - no special config going on to make this work. The PC i'm running has dual NIC, so I have a single network cable connected between one NIC and the teensy, the other NIC is for my normal network.

I setup your teensy board as per your instructions and then did the following for Ethernet to set a static IP for that single NIC/network...

```
$301=0
$302=192.168.60.200
$303=192.168.60.1
$304=255.255.255.0
```

Then in bCNC I use the following in the Serial Port Field

`socket://192.168.60.200:23`

And it connects like normal. While its connected its rock solid, I leave bCNC running all the time even when i leave my workshop(however I power down the stepper drivers). Its remained connected like this for weeks without issues.

I noticed that your default $10=511 value seems important for bCNC to run correctly and report correct coords/status.

The only "major" issue I've noticed is if I close bCNC, or close the connection through bCNC, most of the time the ethernet side of the teensy seems to crash and I can't reconnect it until I power cycle the teensy OR I engage a serial connection via USB and call $$ - that seems to "wake it up" so it speak. This issue doesn't effect me so much as I leave bCNC open and connected all the time - but it should be noted nonetheless.

If you have any other questions or testing I can do, let me know, happy to help.

Cheers

Rob

humneraudio, 2021-08-16:
Hi Phil,

Thanks again for producing the hex file for me, especially considering you were rushing to get onto a plane!

The hex loaded up fine, mostly all good, but It looks like gantry squaring is enabled in this build and I don't think there is a $ config to turn it off. I only have a single Y limit switch and don't use the squaring function. 

I've done a work around for now - I connected the Y limit output to the A limit output so they sink to ground via the same limit switch. This tricks grblHAL into thinking there are 2 limit switches and it homes OK now.

And the backlash compensation works perfectly - this was one of the reasons I had for moving to grblHAL. I already optimised my backlash as much as I could mechanically and software compensation makes sense to me to get rid of the rest.

I use delrin acme t8 nuts and got it down to 0.07mm on X, 0.05mm on the Y and 0.08mm on the Z. I entered these into the backlash compensation and the backlash is now gone! So happy this worked straight out of the box.
I've run a few cuts already on it and it's working well. 

Cheers

Rob

phil-barrett, 2021-08-16:
Sorry about that. When I return home I will make new one without ganged Y.
Please remind me around Sept 6.

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

phil-barrett, 2025-03-05:
To bring this question current, with the grblHAL Web Builder, you can now build backlash enabled firmware.

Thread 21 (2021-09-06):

Auto square gantry. Which hex?

Shkolik, 2021-09-06:
Hello.
Could you please help me with right hex for ethernet board. My cnc has 2 motors on Y so I want to use auto square Y when homing. On a board itself I cut 2 connections and bridge other 2 based on manual for ganged Y. Tried to use "3 axis gangY eth quad enc.hex" but homing not working in this configuration at all. Now I flashed "4 axis gangY eth quad enc.hex" and homing working but looks like not squaring - homing sequence ends on Y limit switch, "A" looks like ignored.

Should I change something in HW or flash another hex?

Thank you!

phil-barrett, 2021-09-06:
Sorry for the troubles. The hardware config was intended for use before grblHAL supported dual motor axis. It duplicates the Y signals on B (or is it A?, I'm on the road so can't look at docs). As such, it does not support squaring.  To use squaring,  you will need to undo the 2 changes.  I'm back home later today (yay! 26 days on the road) and can give you more help then.

I will update the manual to note this. Sorry for the waisted effort.

Shkolik, 2021-09-06:
Phil, no reason to be sorry! You did wonderful work with this board! I'm just asking for help, because not really familiar with cnc :) will be waiting for your response with patience.

Than you!

phil-barrett, 2021-09-07:
Got home.  I configured my_machine.h for 3 axis, ganged Y, auto-square and ethernet. If you don't use ethernet, you can just ignore it - no penalty. I have attached the generated .hex file.  You will need undo to the solder configuration in the "Link A Axis to Y" box on the bottom of the board.  Use solder wick to removed the Y bridges and bridge the A ones.

[grblHAL_T41E3XGYAS.zip](https://github.com/phil-barrett/grblHAL-teensy-4.x/files/7118359/grblHAL_T41E3XGYAS.zip)

Here's my_machine.h for reference.
```
/*
  my_machine.h - configuration for IMXRT1062 processor (on Teensy 4.x board)

  Part of grblHAL

  Copyright (c) 2020 Terje Io

  Grbl is free software: you can redistribute it and/or modify
  it under the terms of the GNU General Public License as published by
  the Free Software Foundation, either version 3 of the License, or
  (at your option) any later version.

  Grbl is distributed in the hope that it will be useful,
  but WITHOUT ANY WARRANTY; without even the implied warranty of
  MERCHANTABILITY or FITNESS FOR A PARTICULAR PURPOSE.  See the
  GNU General Public License for more details.

  You should have received a copy of the GNU General Public License
  along with Grbl.  If not, see <http://www.gnu.org/licenses/>.
*/

// BOARD_T40X101 and BOARD_T41U5XBB by Phil Barrett: https://github.com/phil-barrett/grblHAL-teensy-4.x

// NOTE: Only one board may be enabled!
// If none is enabled pin mappings from generic_map.h will be used
//#define BOARD_T40X101
#define BOARD_T41U5XBB
//#define BOARD_T41U5XBB_SS // For a modified T41U5XBB board, allows spindle sync to be enabled.
//#define BOARD_T41BB5X_PRO
//#define BOARD_CNC_BOOSTERPACK
//#define BOARD_MY_MACHINE // Add my_machine_map.h before enabling this!

// Configuration
// Uncomment to enable, for some a value > 1 may be assigned, if so the default value is shown.

/*
              Plugin: | ETHERNET¹ | SDCARD¹ | KEYPAD | EEPROM | N_AXIS |
----------------------|-----------|---------|--------|--------|--------|
BOARD_T40X101         | no        | no      | yes    | yes³   | max 4  |
BOARD_T41U5XBB        | yes       | yes     | yes    | yes³   | max 5  |
BOARD_T41BB5X_PRO     | yes       | yes     | yes    | yes    | max 5  |
BOARD_CNC_BOOSTERPACK | yes²      | yes     | yes    | yes    | max 3  |

¹ Teensy 4.1 only
² External magjack.
³ EEPROM is optional and must be added to the board.

N_AXIS has a default value of 3, edit grbl\config.h to increase.

*/

#define USB_SERIAL_CDC      2 // 1 for Arduino class library and 2 for PJRC C library. Comment out to use UART communication.
//#define USB_SERIAL_WAIT     1 // Wait for USB connection before starting grblHAL.
//#define BLUETOOTH_ENABLE    1 // Set to 1 for HC-05 module. Requires Bluetooth plugin.
//#define SPINDLE_HUANYANG    1 // Set to 1 or 2 for Huanyang VFD spindle. Requires spindle plugin.
//#define QEI_ENABLE          1 // Enable quadrature encoder interfaces. Max value is 1. Requires encoder plugin.
#define ETHERNET_ENABLE     1 // Ethernet streaming. Requires networking plugin.
//#define SDCARD_ENABLE       1 // Run gcode programs from SD card, requires sdcard plugin.
//#define KEYPAD_ENABLE       1 // I2C keypad for jogging etc., requires keypad plugin.
//#define PLASMA_ENABLE       1 // Plasma/THC plugin. To be completed.
//#define MCP3221_ENABLE      1 // Enable analog input via MCP3221 ADC.
//#define PPI_ENABLE          1 // Laser PPI plugin. To be completed.
//#define ODOMETER_ENABLE     1 // Odometer plugin.
//#define OPENPNP_ENABLE      1 // OpenPNP plugin. To be completed.
//#define FANS_ENABLE         1 // Enable fan control via M106/M107. Requires fans plugin.
//#define EEPROM_ENABLE       1 // I2C EEPROM support. Set to 1 for 24LC16(2K), 2 for larger sizes. Requires eeprom plugin.
//#define EEPROM_IS_FRAM      1 // Uncomment when EEPROM is enabled and chip is FRAM, this to remove write delay.
//#define SPINDLE_SYNC_ENABLE 1 // Enable spindle sync support (G33, G76). !! NOTE: Alpha quality - enable only for test or verification.
                                // Currently only available for BOARD_T41BB5X_PRO and BOARD_T41U5XBB_SS.
//#define ESTOP_ENABLE        0 // When enabled only real-time report requests will be executed when the reset pin is asserted.
                                // Note: if left commented out the default setting is determined from COMPATIBILITY_LEVEL.

// If the selected board map supports more than three motors ganging and/or auto-squaring
// of axes can be enabled here.
//#define X_GANGED            1
//#define X_AUTO_SQUARE       1
#define Y_GANGED            1
#define Y_AUTO_SQUARE       1
//#define Z_GANGED            1
//#define Z_AUTO_SQUARE       1
// For ganged axes the limit switch input (if available) can be configured to act as a max travel limit switch.
// NOTE: If board map already has max limit inputs defined this configuration will be ignored.
//#define X_GANGED_LIM_MAX    1
//#define Y_GANGED_LIM_MAX    1
//#define Z_GANGED_LIM_MAX    1
//

#if ETHERNET_ENABLE > 0
#define TELNET_ENABLE           1 // Telnet daemon - requires Ethernet streaming enabled.
#define FTP_ENABLE              1 // Ftp daemon - requires SD card enabled.
#define WEBSOCKET_ENABLE        1 // Websocket daemon - requires Ethernet streaming enabled.
#define NETWORK_HOSTNAME        "GRBL"
#define NETWORK_IPMODE          1 // 0 = static, 1 = DHCP, 2 = AutoIP
#define NETWORK_IP              "192.168.5.1"
#define NETWORK_GATEWAY         "192.168.5.1"
#define NETWORK_MASK            "255.255.255.0"
#define NETWORK_TELNET_PORT     23
#define NETWORK_WEBSOCKET_PORT  80
#define NETWORK_HTTP_PORT       80
#endif

```

Shkolik, 2021-09-07:
Thank you! I already build my own, but for some reason build ends with error when I enable encoder (#define QEI_ENABLE 1). Without this param everything works. Have no idea - maybe it's a bug or maybe it's me doing something wrong :) Could you try to build the same configuration (3 axis, gangY + auto square Y+ network) + encoder?

Thanks for your help! It's invaluable!

phil-barrett, 2021-09-07:
Yeah, I am getting a bunch of errors.  Maybe Terje did not update the encoder source code.  I put some effort into it tomorrow - fading fast from  27 hrs in transit.

phil-barrett, 2021-09-08:
Here is a link to the issue - it is being fixed and [here is a work around](https://github.com/grblHAL/iMXRT1062/issues/13) for you if you don't want to wait.

Shkolik, 2021-09-08:
Will try today. Thank you!

Shkolik, 2021-09-10:
> Here is a link to the issue - it is being fixed and [here is a work around](https://github.com/grblHAL/iMXRT1062/issues/13) for you if you don't want to wait.

Workaround kinda works but only with 4 days old code. Now repository for teensy produces even more errors. Looks like Terje  doing refactoring.

phil-barrett, 2021-09-10:
Here's a build with the workaround that Terje suggested.  3 Axis, Y ganged to A, encoder, ethernet.
[grblHAL_T41E3XGYAETHQEI.zip](https://github.com/phil-barrett/grblHAL-teensy-4.x/files/7145227/grblHAL_T41E3XGYAETHQEI.zip)

Shkolik, 2021-09-10:
Thank you, I was able to build it myself.

Closed 2021-09-10.

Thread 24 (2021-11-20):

Using an inductive proximity sensor as a limit switch

molove, 2021-11-20:
Hello

Not an issue per se, but a request for help.
I'm a bit of a noob when it comes to electonics/arduinos etc.

I have the breakout board which I've soldered up and am in the process of building an Openbuilds Sphinx type cnc, I would like to make use of grblHAL's auto square function and would like to use proximity sensors instead of limit switches.

I'm not entirely sure how they work but I assume that normally the limit switches just short the limit input to ground.
I have watched this youtube vid https://www.youtube.com/watch?v=F7BjZElStfQ so know how get the output of the inductive sensor to 5v. If I take the power for the inductive sensor from the same supply as the 12v input and using a suitable pulldown resistor on the sensor output, do I just connect the sensor output to the limit input, and when the sensor output goes low it triggers the limit input?

I don't want to damage the board or teensy by sticking 5v onto an input that might not be expecting it.

Great job with the board btw, really quick delivery to the UK.

TIA

Piers

phil-barrett, 2021-11-20:
Thanks for linking to that video.  Worth watching.  The inputs for the limit switches are looking for 5V, anything below 5.25V will be good. The 2K he uses in the video is a bit low, try 2200 or 2700 to get the voltage to a little below 5V.  You can go as low as 4.25V without any problems.

Note that the actual resistor value will be dependent on the pull-up resistor in the sensor. They are all going to be different so you will have to experiment with yours like in the video.

To answer your direct question, yes, you would put a resistor between input and ground along with the sensor input and common ground.  If you use 22 Ga wires, you should be able to inset both the resistor lead and senor wire into the screw terminals.  I recommend using a ferrule to keep the wires together. 20 Ga ferrules are a bit tight but can be made to fit the screw terminals.

phil-barrett, 2021-11-20:
Here is the github discussion on this.
https://github.com/phil-barrett/grblHAL-teensy-4.x/issues/24

I may do a blog on this topic.

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

molove, 2021-11-20:
Thanks for the swift reply, and confirming I had understood correctly.

 I will adjust the resistor to match my sensor so it's outputting less than 5.25V. And yes I'm very fond of a ferrule and try to use them for all my projects.

I'm sure there will be more questions that I have as I set up my machine, that won't be "issues" as such. Is there a proper forum to ask them on, or should I just ask here?

phil-barrett, 2021-11-20:
You are welcome and, yes, you got it right.

I enabled discussions for this repository. So, [you can ask them here](https://github.com/phil-barrett/grblHAL-teensy-4.x/discussions).

stevempotter, 2021-11-21:
@molove, see my post on here on the Discussion forum about using Hall Effect switches as endstops.

molove, 2021-11-21:
@stevempotter I'm not sure where I'm meant to be looking for your post, can you let me have a link?

phil-barrett, 2021-11-21:
> @stevempotter I'm not sure where I'm meant to be looking for your post, can you let me have a link?

It's [here, scroll down a bit.](https://github.com/phil-barrett/grblHAL-teensy-4.x/discussions/25)

humneraudio, 2023-05-22:
With regards to NPN proximity sensors, which is best between NC or NO?

phil-barrett, 2023-05-22:
It is a bit complex. If you are only going to use one per axis, then either NO or NC. However,  if you will be using 2 per axis, then NO is better. This assumes that you are using sensors with open collector outputs.

humneraudio, 2023-05-22:
no worries, thanks. it will be a single sensor per limit input.

humneraudio, 2023-08-21:
I thought I would just use this to continue with this discussion. I setup the NPN NC proximity sensors and used resistors to get the same 5 v output for the BOB. I used a 12v SMPS for the proximity sensors.

I prefer to have the microusb powering the BOB via my raspberry PI - however I found the proximity sensors don't work in this config. I assume its because both grounds are floating?

If I power the BOB/teensy via a 5v buck converter on the 12v SMPS - it all works ok as it appears the GND is linked.

However I still have a preference for the raspberry PI to power the teensy.

Does that mean I should connect the GND from the 12v SMPS to the GND of the BOB/teensy if its connected to the Raspberry PI to make it a common GND point?

Is that safe?

phil-barrett, 2023-08-21:
Yes, it is safe to connect the two grounds.  They need a common ground otherwise the sensor voltage is not referenced to the ground of the breakout board (which is the Pi's ground, too).

humneraudio, 2023-08-25:
thanks phil. I had a chance to play around with it today, however joining the grounds didn't have any effect or change while the breakout board was connected to the Raspberry PI.

I think I need to take a step back and double check my wiring before i continue.

humneraudio, 2023-08-26:
long story short, it was a wiring fault. And in the process, I also found that I had tied the ground of the breakout board to chassis ground via a DIN cable I made years ago for the halt/start/hold buttons. I had tied the DIN cable shield to the ground connection within the cable itself. No idea why I did that, but have at least solved some mysteries.

Closed 2025-03-05.

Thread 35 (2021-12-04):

Question and or project

Cncninja, 2021-12-04:
Hello Phil,

I have one of your Teensy boards and want to use TMC drives. have you thought about this as a project i know so many people would jump on it

"Hello in trying to use TMC drives with a Mini CNC mill. the control simply has step and dir output. I know i can run them in standalone mode but wonder if there is a project out there where an Arduino could be set up to just configure the drive and show status on a mini OLED. but the step and dir signal come from the CNC control I know 3d printer software is an all-in-one solution, but Mach3/GRBL/UCCNC/LinuxCNC/Acorn(CNC mill software) has no or little support. if there was a way to simply have a separate Arduino plug into the UART/SPI and handle the config only that would enable CNC mills to take advantage of more features such as setting stall guard and using the Diag pinout for homing switch input etc. Has this been done? If not I would be willing to pay for help to make this a reality. i Imagine a small box with OLED that can simply plug into the Uart/spi and a few menu buttons and leave the step/dir to the CNC motion controller. Some features I would like to use would be sensorless homing, spread cycle threshold, current, micro-stepping resolution. Thanks for any help and input.

I think it would work well with these holders.

https://www.amazon.com/gp/product/B08LMSYXVF/ref=ppx_yo_dt_b_asin_title_o02_s00?ie=UTF8&psc=1

There is a TMC library for Arduino already I just have zero code skills.

https://github.com/teemuatlut/TMCStepper

phil-barrett, 2021-12-04:
I have looked at it.  There are lots of really cheap boards that support step sticks though most do not support the TMC extensions.  Have you looked at the grblHAL plugins for TMC? I know that Terje has a board that supports the Nucleo dev board series and has TMC support.  There is also grblHAL support for the SKR series which has the sockets (though I'm not sure about TMC support).

I have played with supporting the format.  It would take a completely new board.  What I don't know is if there is a decent market.  Lots of boards that support the format so I'd just be one small voice in a gale of products.

Closed 2025-03-05.

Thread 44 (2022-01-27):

Ethernet Pairs used

gxdeange, 2022-01-27:
Hi phil-barrett,

Just a quick question regarding the wire pairs used in the schematic for ethernet connectivity.

I noticed you are using pairs 2 (Green) & 4 (Brown) but I suspect it should be pairs 2 (Green) & 3 (Orange).

This is based on T-568a.

Cheers
George

phil-barrett, 2022-01-28:
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

Thanks for the comment.

To be honest, I am not sure there is a problem.  This is standard networking with the Teensy 4.1.  Many people ( multi hundreds) are using the T41 breakout board with Ethernet.   And a lot more people are using Ethernet with the Teensy 4.1 plus the PJRC Ethernet kit which uses the same wiring as I do.

gxdeange, 2022-01-29:
OK. I just realised that this is not a standard RJ45 jack.

I also noticed this diagram which I believe is the PJRC Ethernet kit schematic.

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

Can you please confirm this is what you have used?

Cheers
George

phil-barrett, 2022-01-29:
That's not the specific magjack I use but yes, it's not an plain RJ45. It has integrated magnetics. There is no standard for magjacks - every one is slightly different so there is no interoperability.

gxdeange, 2022-01-29:
Awesome. I found a MagJack with equivalent parameters but slightly different pin assignments.

Cheers and have a great day
George

phil-barrett, 2022-01-30:
By the way, in the manual for the Teensy BOB, I have the part number of the I use in the BOM.

karoria, 2022-01-30:
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

There are magjacks with 2 or 3 types of pin assignments in the market. You can check continuity by multimeter to see which pin diagram is suitable for what you have. Pins connected with coils should show continuity.

Closed 2022-01-29.

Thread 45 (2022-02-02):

Vacuum controls trouble shooting

Drew265, 2022-02-02:
The capability of this board has motivated me to incorporate dust collection onto my machine. I added a relay to control a small shop vac and attached the relay to the TTL/SSR Relay pins labeled VAC/DC. The vacuum cycles on and off with the spindle as intended.

I then attached a switch to the Vac/DC Trigger pins and that is where my trouble begins. The vacuum does not turn on when the switch is toggled. I have done the following to find the problem.

1. Check the switch is working correctly.
2. Checked pin 1 of JP8 for 3V.
3. Checked pin 2 of JP8 to ground for 100K resistance.
4. Checked continuity between pin 2 of JP8 to IC16.

My assumption is that because spindle enable also feeds into IC16 that everything from this point on is working correctly.

Is that assumption fair?
What additional checks should I perform to trouble shoot this issue or is the problem accurately assessed to be within IC16?

phil-barrett, 2022-02-02:
The switch should work. Spindle enable and the VAC/DC Trigger pin header (pin 2) feeds into an OR gate (IC16). Pulling pin 2 to 3.3V (i.e connecting to pin 1) should cause the the output of the OR gate to turn on the VAC Relay output.  If Spindle Enable is doing that, the OR gate is working. You said pin 2 connects to IC16 (top left pin of IC16, when looking at the board with the Teensy to the left) and pin 1 reads 3V (probably closer to 3.3V). That is as it should be.

Are you sure the switch is working and the wires are connected correctly to the switch?  Given what you said above, that seems like the most likely cause. Try carefully shorting the two pins with a small metal screw driver to see if the relay turns on.

Drew265, 2022-02-03:
Thanks for the quick response! Yes, I measured 3.3v not 3 like you suggested.
I placed a jumper across the pins where the switch connects to the board and the relay does not turn on. An interesting observation, while the jumper was installed, I turned on the spindle just to see what would happen and the vacuum did not turn on. I then removed the jumper while the spindle was still on and the vacuum turned on.
And then the light bulb came on.... I reversed spindle enable in the GRBL settings ($16=1).
I changed $16=0 and the vacuum works correctly with the switch.
Looks like I need to rethink how I have the spindle setup.  I will clean that up and see if I can get everything working together.

Thanks a lot Phil, I would not have gotten this far without your explanation of the circuit.

phil-barrett, 2022-02-03:
Glad to help.  Yes, you will need to have spindle enable not inverted to be able to use the vac switch.  Though, I don't understand why the vac wasn't running when the spindle was off with spindle enable inverted. I will have to set that up an look at it.

Closed 2025-03-05.

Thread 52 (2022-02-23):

Alarm:10 error on First launch attempt with grblHal 2.0.36

pierrerdurand, 2022-02-23:
### Discussed in https://github.com/phil-barrett/grblHAL-teensy-4.x/discussions/51

<div type='discussions-op-text'>

<sup>Originally posted by **pierrerdurand** February 23, 2022</sup>
Have a new grblHal breakout board v2.07 fully built.
Have uploaded the 'grblHAL_T41 3X qei.hex' with the Teensy loader.
Installed ioSender 2.0.36 on windows 11
Have one DM556 stepper controller connected to the X axis connections with a bi-polar CUI stepper attached to the stepper controller.
Nothing else is connected to the board other than the USB power from the windows PC.
When I launch ioSender 2.0.36 (with the DM556 attached or not attached) I get the ALARM:10 error: "E-Stop active! - clear before continuing..."
After acknowledging the message, I get E-Stop still active, exit?" message and am unable to to any other actions.
What I am doing wrong?

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

</div>

phil-barrett, 2022-02-23:
[Answered here.](https://github.com/phil-barrett/grblHAL-teensy-4.x/discussions/51)

Closed 2025-03-05.

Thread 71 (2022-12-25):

Connecting T41U5XBB to a servo drive

tonluc123, 2022-12-25:
Hello,
My goal is to run T41U5XBB with a servo drive. So far I run T41U5XBB with steppers and it runs perfect. The servo drives and motors that I have available are Siemens V90 and they accept signals 24v or High-speed 5 V differential pulses. I tried driving directly with Teensy firmware and T41U5XBB but I'm missing pulses. My thought is that since I have not differential pulses it would be a good idea to amplify the 5 signals to 24v since no differential signals are needed at this drives input. My question (request) is this: what is the best way to go ?
High speed optocouplers, high speed transistors ? Any suggestions are welcomed.
Lucas

phil-barrett, 2022-12-25:
Hmmm, could you give me a link to the manual or datasheet for the servo controller?  It might be as simple as increasing pulse width but lets see the servo wants.

tonluc123, 2022-12-26:
Hi Phill, Merry Christmas,
This is the link (page 60) https://cache.industry.siemens.com/dl/files/218/93005218/att_74528/v1/SINAMICS_V90_OPI_en-US_en-US.pdf
I do not think the pulses width is the problem, I have driven it with a PLC and checked with an oscilloscope, at high speeds the width is the same (I'm not able to do this right now and verify it again).
Thanks for your fast response.
Lucas

phil-barrett, 2022-12-26:
Looked through the manual.  Whew! Now that's DOCUMENTATION.

I wasn't able to see if it actually takes simple step/dir/enable signals but assume that is possible. Maybe there is a separate interfacing document.

It could be output signal drive from the T41U5XBB - it should handle 10 mA. But if the input optos of V90 expect higher voltage, it could be they have higher resistance that drops the current.  FWIW, I have never seen this problem with the T41U5XBB after shipping over 1000 units.

I would use a simple driver circuit using an NPN transistor or something like a ULN2003 (which has 7 drivers in a single package). You'd need to invert the signals in the Grbl settings. Since the V90 already has optos inside, you don't need to worry about that.  I can work up a circuit drawing if you need.

tonluc123, 2022-12-26:
Phill,
Yes the drive has step/dir/enable signals. The drive has different inputs for 5 and 24vdc (High-speed 5 V differential pulse train input (RS485)Maximum frequency: 1MHz=1-2 steps & 26-27 dir) and (24 V single end pulse train input Maximum frequency: 200 kHz 36-37 steps & 38-39 dir). Of course this is not a T41U5XBB problem, this board was designed for steppers and their drives and as I said it works fine with them. ULN2003 was my first choice regarding voltage and speed but I'm not sure how to implement it in this case. If you can help me it would be great.
Lucas

phil-barrett, 2022-12-26:
By 5V differential, I think that means 2 wires per signal. when one wire is +5V, the other is 0V.  (and not -5V). Looking through the manual, I'm not sure which inputs are step and dir - are they the inputs in section 4.3?  It looks like they are talking about the encoder pulse stream.

tonluc123, 2022-12-26:
Yes they are the inputs described at section 4.3. This manual looks like it was written for rocket scientists, I was fighting for hours to understand what the author meant to say. Anyway those inputs are not for the encoder connection. For 5v the step inputs are #1&2 and for dir #26&27. If you want I can send you photos by mail.

tonluc123, 2022-12-26:
Phil,
I just found this https://cache.industry.siemens.com/dl/files/415/109757415/img_249458/v1/2_en.png
Hope it helps a little

phil-barrett, 2022-12-27:
OK, makes more sense now.  I see 2 approaches:

1. 5V differential - use 1, 2, 26 and 27.  Use inverting drivers to create differential from single ended 5V output from T41U5XBB.
2. Create single ended 24V from 5V single ended.

Either one should work.  #1 may be simpler in that you will not need to supply 24V.

For #1, I would use an inverting line driver.  The [MC74VHC540](https://www.mouser.com/datasheet/2/308/MC74VHC540_D-1811369.pdf) is an 8 channel inverting with high drive capability and 3.7 nS switching time.  For each single ended signal, I would input it to a channel (say A1) and then connect Y1 (the output) to A2 to derive the differential signal.  So, Y1 and Y2 are your differential signals to feed into the V90.  Repeat that for each additional signal.  Each 74VHC540 will allow you to do 4 singled ended signals.  This should work up to about 200 kHz step rate.

For #2, use a ULN2003 to boost to 24V.  Since the '2003 is open collector, I would connect to output to the ground level of the v90 input and +24V to the signal input.  The '2003 will pull the voltage low via the signal's ground pin.

Let me know if you need me to draw up the circuits.

tonluc123, 2022-12-27:
Hi Phil,
I feel a bit stupid, I read those 2 posts but I don't se how are they related with my case (my English maybe). I liked though the solution of MC74VHC540 and even with a ULN2003 (easier to find) . A circuit would be great if it is not too much for you.
Lucas

phil-barrett, 2022-12-27:
Here's what I worked up. Note that this is for a single servo.  Repeat for each additional servo.  Note that common ground is NOT needed. In fact common ground will defeat isolation.

The single to differential conversion speed max is probably greater than 1 MHz (unlike what I said earlier).  5V to 24V speed is around 1 MHz.

I would prototype with this first. Let me know how it goes.  I am thinking of creating a board that people can get made.
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

tonluc123, 2022-12-28:
This is great Phill, I have a minor question about ULN2003, how do you power it ?
From my side I'm thinking for an easier solution with a BS170 (24v driver), https://www.onsemi.com/pdf/datasheet/mmbf170-d.pdf it has 10ns turn on & turn off time. I used an oscilloscope at T41U5XBB yesterday at normal speeds and I had 10 μs pulses. I believe it will work. Of course the solutions you propose are much better and the case of 74lvt240 much more professional.
Did you check this https://cache.industry.siemens.com/dl/files/415/109757415/img_249458/v1/2_en.png by the way? What do you think, is it differential or common ground ?

phil-barrett, 2022-12-28:
You can use individual FETs (or bipolar transistors).  The ULN2003 is actually made up of transistors. Each channel is a pair of transistors in a Darlington configuration. See the diagram below.  I like it because it is simple to use and has some protections (like against start up glitches). If you use the FET approach, be sure to pull the input low with a 5 to 10K resistor to prevent glitches at start up. Also, limit the base current to something like 6 mA to be safe.
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
You don't power it in the sense of a conventional IC. It works similar to your FET in that the input signal turns on the darlington pair which connects the output pin to ground.  So you connect your "load" between +V and the output pin like so
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
In this case the load is an opto isolator (very likely what is in the V90).  When the input (or base) signal goes high, current will flow through the load (opto in this case).

The doc you referred to shows that differential needs a common ground so I would go with that.  But, it is silent about single ended so I would try without common ground first and if that doesn't work, then connect the ground.

tonluc123, 2022-12-29:
Hi Phill,
This is the result with BS170, I see some attenuation at the rising edge I drive the gate with 1k in series and 5k to the ground.
I would appreciate your opinion with this approach.
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

phil-barrett, 2022-12-29:
That looks like it should work. Most signals are not ideal and it depends on the capacitive load you are driving. You'll never see perfect square waves. Have you tested it with a load (either an opto, led or resistor)? See fig 11 in the datasheet. I would also put a small resistor (50 Ohm) in series with the drain to protect against shorts.  FETs can be fragile.

tonluc123, 2022-12-29:
And this is the ULN2003, the rising edge looks more or less the same with the one of Bs170
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

tonluc123, 2022-12-30:
Phill,
I have tested it with a resistor, as for perfect squares, your board outputs perfect squares (professional work, congratulations).
I may be able to improve the output as I solder the drive on a prototyping board and non shielded cables.
In any case thanks a lot for your help with this (as it was not really an issue) and keep the good work.
Happy new year
Lucas

Closed 2023-01-24.

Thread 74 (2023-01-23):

Some help please

tonluc123, 2023-01-23:
Hi Phill,
I obtained Eth. kit for Teensy (MagJack) and tried with a "naked T4.1 with no success. My hex file was build from: http://svn.io-engineering.com:8080/ with tall the network options. After reading some articles I was confused and decide to ask for some help.
P.S. With ## Teensy 4.1 ethernet :: https://forum.pjrc.com/threads/59776-Ethernet-and-lwip , and an example I can see that hardware is in order and I have feedback to my serial monitor.
Your help is appreciated.
Lucas

phil-barrett, 2023-01-23:
What Eth kit did you get?  mine or from PJRC?

Also, I don't quite follow your naked T4.1 reference.  How are you hooking up the magjack if it is not on the breakout board?

tonluc123, 2023-01-23:
Hi Phill,
I got the the PJRC  kit. Naked means not at your board, it is connected with a ribbon cable (teensy to eth board).
No I have not tried the prebuild ones , I will in a short while
Lucas

phil-barrett, 2023-01-23:
OK, let me know what you find.  Also FIY, the PJRC kit will not work with the T41U5XBB - the magjack pinout is wrong.

tonluc123, 2023-01-23:
Just tried, no luck. I thought that you use the same rj45 connector with pjrc. Is it possible to find one of yours in Europe ?

phil-barrett, 2023-01-23:
Hmmm, do you have the Ethernet Teensy 4.1? There are 2 versions - one without ethernet.  You can tell by looking at the 6 pin 2mm header - there should be a small chip between the header and the MXRT1062 chip.

As long as you use the PJRC board/cable combo and connect it correctly, it should work. Maybe check cable orientation? How did you verify the HW earlier?

tonluc123, 2023-01-24:
Yes it is an Ethernet Teensy 4.1. As I mentioned before I can verify that everything works fine by testing it with library's examples. Most probably It has to do with mistakes I do of how to apply the code. If everything that I need is included at the hex file that I downloaded from http://svn.io-engineering.com:8080/  and no further action is needed it should work. Please forgive me, I'm not a networks specialist maybe I miss something basic that I'm not aware of.

phil-barrett, 2023-01-24:
Ok, I think the problem is not with the ethernet support but maybe with your io builder options.  Try this json file.  Load it into the builder and build.  I was able to load the resulting .hex file.
[iMXRT1062_T41U5XBB.zip](https://github.com/phil-barrett/grblHAL-teensy-4.x/files/10492571/iMXRT1062_T41U5XBB.zip)

tonluc123, 2023-01-24:
How do I flash the json file ?

tonluc123, 2023-01-24:
Phill I just managed to connect: used static ip instead of dhcp. Can you understand why is this ?
Lucas

tonluc123, 2023-01-24:
Can I send you pm ?

phil-barrett, 2023-01-24:
Use email - phillip dot lyne dot barrett at gmail.com

phil-barrett, 2023-01-24:
If you are connected, go into Grbl settings in ioSender.  Under network select dynamic for dhcp.  Not sure why your build was set to static.  Mine was set to dynamic.  Could have been an earlier setting.

tonluc123, 2023-01-24:
Thanks for been so helpful

Closed 2023-01-24.

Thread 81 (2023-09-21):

Teensy 4.1 DEV-16771 + lightburn

distebia, 2023-09-21:
Salve, ho intenzione di passare da mks dlc32 esp32 a Teensy 4.1 DEV-16771 e usare grblhal...posso continuare ad usare la licenza gcode di lightburn oppure devo aggiornare la licenza?

phil-barrett, 2023-09-21:
Please forgive my lack of Italian...

I have an older version of Lightburn but believe all you have to do is click on the devices button. Try Create Manually and select Grbl.  I think you can test it right now.

distebia, 2023-09-21:
salve e grazie per la risposta...non ho ancora comprato la scheda T41U5XBB e aggiungere il Teensy 4.1, non so come muovermi in quanto non trovo la T41U5XBB in europa, ma mi piacerebbe entrare in questa avventura. la mia domanda era inerente alla versione di lightburn da utilizzare, la versione base per gcode oppure quella dsp?

phil-barrett, 2023-09-21:
Ah, yes.  The Basic Version.

You can purchase the T41U5XBB from  [tindie.com](https://www.tindie.com/stores/philba/).

distebia, 2023-09-21:
ok per la versione. Avevo visto il sito e ho anche chiesto quale era la differenza di prestazioni, per uso laser co2, non cnc con mandrino ed interferenze) fra la versione usb e ethernet. inoltre il Teensy 4.1 non è fornito nel kit, vero? esiste un modo per comprare il prodotto da un negozio in europa? le spese doganali incidono tanto, oltre al trasporto

phil-barrett, 2023-09-21:
Ethernet vs USB - Ethernet is same speed as USB.  Ethernet has isolation for anti-EMI.  But, Lightburn Version 0.94 does not support Ethernet for Grbl, only USB.  I do not think they have changed that for Version 1.0 and later.

Tindie is the only source for T41U5XBB.  Sorry for the expensive shipping, I can not do anything about that.

distebia, 2023-09-22:
ok, mi sono quasi convinto per l'acquisto della sola scheda, kit base di $ 29.99, solo che mi serve sapere con esattezza cosa devo aggiungere, magari avere il termine tecnico per trovare il giusto connettore e pin a saldare. Altra domanda...l'alimentazione della scheda avviene tramite cavo usb, quindi dal pc, del Teensy 4.1? La mia configurazione (autocostruita) di 1300x1000 attualmente è composta da mks dlc32 che comanda 3 tb6600 che comandano 3 17HS8401S. Tutto scorre su guide lineari di 20mm con relativi pattini, nessun problema qua.
Passando al VS progetto avrò problemi con la mia meccanica, nel senso che i motori o i driver sono pensati per una macchina + lenta?

phil-barrett, 2023-09-22:
You can power it from USB, a USB charger (if you use ethernet) or external 5V. If you want to use 0-10V to control a spindle or drive 12V relay coils, you will need to supply 12V also.

You should probably take a look at ordering the USB assembly kit as that has all the connectors you will need. Make it very easy to get up and running. If you do not mind ordering the connector parts separately yourself, the user manual has a bill of materials for it.

I do not see any problem converting over - your mechanics sound fine. You can make the board run at the speed that they need.  You should write down all of your Mach3 settings before switching.

phil

distebia, 2023-09-22:
ho trovato online un teensy 4.1 completo di pin saldati ai lati (24+24) e la connessione 2x3 2mm ethernet gia saldato nel teensy 4.1. la differenza di kit da usb a ethernet è il connettore ethernet + il pin 2x3 2mm? oppure qualche altra cosa? circa l'alimentazione non trovo niente online. attualmente utilizzo relè 3.3v...devo usare 5v? dopo l'acquisto posso chiedere eventuali dubbi per il montaggio, firmware e altro?

phil-barrett, 2023-09-22:
The Ethernet kit has the MagJack, 2x3 2mm header and 2x3 2mm socket.  Be aware that if you buy a MagJack separately, you need to get the exact part number. There is no standardization.

The 2x3 2mm header will have to match the socket.  I think it will be ok but the ethernet pins need to be the same length as the other 24 pins on the sides of the teensy.  Could you send me a link?  Soldering 2mm pins is a lot harder than 2.54mm for some of my customers.

distebia, 2023-09-22:
ok per il MagJack...che succede se inserisco il Teensy 4.1 e saldo i 24+24 + i 2x3 2mm e non connetto il magjack? non saldo completamente il MagJack. Non saldando il connettore ethernet semplicemente non ho ethernet o, magari, il jak chiude qualche circuito?

phil-barrett, 2023-09-22:
A bad connection will not cause any problems other than no Ethernet.

distebia, 2023-09-23:
scheda comprata, grazie per i consigli...ci risentiamo quando arriva la scheda e il teensy per l'installazione di grblhal. Grazie

distebia, 2023-10-01:
Salve, per collegare un sensore pnp no con 5v-s-g
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
posso collegarlo quà?
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

distebia, 2023-10-01:
Altro quesito: per collegare un relay devo usare necessariamente 5v? non posso usare 3.3v come per mks dlc32 (esp32).
Per un 5v immagino di collegarlo in questo modo:
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
Fornisco esternamente 5v nel connettore in basso e alimento tutta la scheda, mettiamo 5v 1A?, imposto il selettore 5-12v su 5v mediante jumper, prendo un qualsiasi G e lo porto al G relay, prendo dalla sezione Mist +V e lo porto a V del relay e S dal relay lo posto a Mist?
Inoltre alimentando esternamente la scheda penso che devo modificare il cavo usb che va al pc..interrompo nel cavo il 5V ottenendo un cavo usb con 3 fili (-D, +D e G)

phil-barrett, 2023-10-01:
For the PNP sensor.  The connections you show are ok but I have not tested it with PNP sensors.  By the way, optical sensors like you show can be false triggered by debris (saw dust? swarf?  I don't know the Italian word for that).

On relays, no 3.3V option is available.  What you wrote works to drive actual relay coils.  You do not need to modify the USB cable.  You can cut the USB solder jumper trace on the Teensy or cut the solder jumper trace on the bottom of the T41U5XBB.  I recommend cutting the Teensy.  But, If you are using powered Relay modules, you should use the TTL outputs instead of the relay outputs. The relay outputs are for directly driving relay coils.

distebia, 2023-10-01:
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
dentro ho sia relè 3.3v che 5v come questo. userò il 5v. suppongo che mediante il pin S non vado ad alimentare direttamente la bobina...in questo caso devo usare le uscite ttl e non relè? quindi S dal modulo relè lo collego qua?
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
Ma il .hex generato da web build prevede Mist su questo pin? o devo modificarlo ricompilando?
Circa i PNP quando impegnato ho 5V su S, invertendo il $5 risolvo?
Non mi va di rovinare la scheda tagliando tracce e ponticelli, L'alimentazione è esterna e non mi serve da usb...dovrebbe funzionare lo stesso...o mi sbaglio? se sbaglio posso sapere quale traccia tagliare?

phil-barrett, 2023-10-01:
You are on the right track but use the Gnd (G) next to the Signal (sig).
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

phil-barrett, 2023-10-01:
scusatemi, avrei dovuto postarlo prima.
https://www.grbl.org/single-post/using-relays-with-grblhal-and-the-t41u5xbb

distebia, 2023-10-01:
Grazie per la guida dei relè, ben fatta. Per quanto riguarda  i PNP posso usarli invertendo la logica di $5 ? In questo momento alimento la mia mks dlc32 con 12v e, per non stravolgere l'elettronica, posso alimentare la T41U5XBB con 12V, commutare il jumper su 5V per usare i relay a 5V con le connessioni indicate?
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
 Inoltre il pin da usare per comandare un laser, Co2 oppure diodo, è quello indicato in figura?
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
distebia, 2023-10-27:
https://www.amazon.it/dp/B0BP5BNC9K?psc=1&ref=ppx_yo2ov_dt_b_product_details

questo è il teensy che ho comprato...parla di ethernet. ho saldato i 6 pin e ho testato la continuità, entrano perfettamente su T41U5XBB e ho continuità. l'unica cosa che ho notato è che il led del rj45 non lampeggia e che il fritzbox non riconosce niente attaccato con il cavo ethernet. domani allego le foto reali del teensy

phil-barrett, 2023-10-28:
That has the ethernet Phy chip on it - right next to the 2x3 2mm header.

distebia, 2023-10-28:
il teensy ha il chip, l'intestazione 2x3 2mm è ok, il socket sotto è ok, il connettore è uguale, il firmware è ok (almeno credo)...cosa è andato storto?

phil-barrett, 2023-10-28:
When you plug the ethernet cable in to a router/switch, does the port light turn on? Also, one of the LEDs should start flickering when connected to a working ethernet.

On the other hand, perhaps you could find the RB1-125BAG1A magjack in the EU? They are fairly common and not terribly expensive.

distebia, 2023-10-28:
I led non si accendevano e non lampeggiavano, comunque ho smontato il connettore e messo da parte. Ho notato invece che alla fine del lavoro il controller rimane in stato occupato. La macchina è sempre la stessa e prima con mks dlc32 non succedeva. Succede anche che quando parte la lavorazione si blocca senza segnalare errore e devo spegnere. All'inizio del lavoro viene acceso il relay ttl e spento alla fine del lavoro, forse è questo? Ho rigenerato il firmware 3 assi solo con LB cluster attivato e devo ancora testare.

phil-barrett, 2023-10-28:
No LED lit means the phy has not been able to establish connection to the ethernet router/switch.

distebia, 2023-10-28:
Devo riprovare saldando nuovamente il connettore. E per i problemi di "stato occupato"?

phil-barrett, 2023-10-28:
I have never encountered busy status so not at all sure what it means.

distebia, 2023-10-28:
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
questo è lo stato occupato, non risponde ai comandi e devo spegnere e riaccendere

phil-barrett, 2023-10-28:
Ah, Lightburn.  I'm not sure what that means.

distebia, 2023-10-28:
Si, sono collegato tramite usb. Lo stato busy si verifica all'inizio e alla fine del lavoro, ma non sempre. il controller va in stallo e non accetta comandi, devo togliere l'alimentazione e riaccendere. Altre volte basta uno stop e tutto riparte senza perdere la posizione. questo problema mi succedeva con arduino, poi ho montato anelli di ferrite sui segnali step e dir che dal controller vanno ai tb6600 e le cose sono migliorate. ho anche aggiunto dei condensatori 275vac x2 (su fase e neutro) di alimentatore laser co2, pompa acqua e compressore aria. con arduino non ho avuto più problemi, sono passato a mks dlc32 e non avevo problemi del genere. Per quanto riguarda l'alimentazione fornisco 5v sui pin della T41U5XBB. Non ho interrotto tracce nel pcb. Utilizzo un cavo usb senza i 5v e funziona. non capisco cosa può essere. Quale altra precauzione posso prendere per evitare questi blocchi?

distebia, 2023-10-29:
ho superato i problemi di stato occupato...era bruciato un condensatore 275vac x2 messo nella pompa dell'aria, infatti mi busy mi succedeva all'inizio e alla fine del lavoro. Ho anche riscontrato problemi con l'alimentazione 5v che fornivo alla scheda, mi mandava in tilt casuale il teensy. attualmente non fornisco alimentazione alla scheda e alimento solo con usb...tutto funziona.
quello che non funziona è la connessione ethernet, non ottengo l'ip e i led non lampeggiano. fra qualche settimana mi dovrebbe arrivate un RB1-125BAG1A non trasformatore interno...

distebia, 2023-11-09:
Purtroppo ritorno al problema dell'alimentazione da scheda...con qualsiasi cosa (lm7805 1.5A +condensatori, alimentatore 5v stabilizzato, alimentatore per ricarica cellulare 5v 2a) il teensy va in stallo durante il lavoro, si congela e non accetta niente, posso solo spegnere. Se alimento da usb tutto perfetto. tutto questo mi succede dopo aver caricato un firmware compilato da me (platformio e senza errori o avvisi). Se carico un firmware generato da web build il problema scompare (almeno credo). Posso riutilizzare i miei alimentatori per fornire 5v alla scheda e cavo usb solo dati verso pc. Mi sembra strano ma è così. Allora penso a qualcosa di sporco che carico io nel teensy, o qualcosa che rimane sporco dopo il caricamento del firmware. I problemi sono iniziati quando ho variato il $398=35 e l'ho modificato a $398=100, dopo questa operazione il teensy non digeriva bene l'alimentazione 5v da scheda. Come posso formattare completamente il teensy? Carico lo schizzo blink e poi il firmware generato da me?

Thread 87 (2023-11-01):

T41U5XBB network connection

Hatty99, 2023-11-01:
Hi Phil,
I'm attempting to connect myT41U5XBB  board to my network.
Have generated and loaded firmware as per your instructions: https://www.grbl.org/single-post/networking-the-t41u5xbb, with Ethernet/telnet/Websocket all checked, and attempted to connect to the board via the network, unfortunately unsuccessfully. As far as I can tell USB connection is working OK. (machine homes and can move with gcode)
The board is connected to the network, and the network connector led is flashing. It successfully obtains an IP address, but there is no message indicating a NETCON connection. I can ping the ip address from my Windows laptop, but am unable to open a connection using telnet from the laptop.
When starting ioSender, the program shows the message "Unable to open connection (ws://192.168.XXX.XXX:80)" showing the correct IP address.
Could you be able to either point me in the right direction or suggest any further diagnostic moves?
Thanks,
Dave.

phil-barrett, 2023-11-01:
Did you close the USB connection?

Hatty99, 2023-11-01:
I believe so. Have disconnected the USB cable and the com port has disappeared from Device Manager. 

When the com port is still open, ioSender connects via USB. When the port is closed I get the "Can't open connection" message.

5v and 3.3v on the teensy board seem ok without the usb connected. 

Hatty99, 2023-11-01:
Thanks for your prompt reply and help Phil. Changing to port 81 has made it work.

Closed 2025-03-05.

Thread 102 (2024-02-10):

calo improvviso emissione laser

distebia, 2024-02-10:
Salve, oggi stavo facendo una lavorazione su 3 livelli colore di lightburn, 1° livello foto modalità stucki, 2° riempimento di contorni e 3° taglio. Il problema si presenta dopo aver fatto perfettamente la foto, finisce la foto e passa al riempimento. Effettua si e no 20 linee di riempimento, impostato a 8000mm/min 20% 0.08 linee per millimetro, e all'improvviso mi accorgo che il laser si muove ma non ho emissione di fascio, l'amperometro da 0-30mA segna forse 2 e nel plexiglass si vede che il riempimento non c'è. Blocco tutto, rifaccio l'homing, seleziono soltanto 2° livello-riempimento e 3° livello-taglio e porto a termine il lavoro. Utilizzo teensy4.1+T41U5XBB. Non riesco a capire da cosa può dipendere tutto questo, la macchina funzionava prima e funzionava anche dopo, è come se il controller abbassa, ma non azzera, l'uscita pwm, dopo l'homing (senza toccare altro, tipo spegnere e rieccendere ecc...) tutto funziona come prima. Anche la temperatura era nel range valido e segnava 13.4 °C

phil-barrett, 2024-02-10:
Sorry to hear of the problem.

Was there any message in the console?  Could you still talk to grblHAL? (for example, send $$, get settings listed back?)

What happens when you run the same job?

distebia, 2024-02-10:
potevo parlare con grblhal, ho premuto stop su LB e ho eseguito l'homing. Niente è stato spento per raffreddarsi, dopo homing ho ripreso subito il lavoro

phil-barrett, 2024-02-10:
OK, keep an eye on the Teensy LED if this happens again.

distebia, 2024-02-10:
ok, l'amperometro segnava, poco ma segnava, era come un'uscita settata al 20% ma eseguita al 1%.

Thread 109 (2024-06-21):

Question about 5V power

JasonTitcomb, 2024-06-21:
Regarding T41U5XBB. v2.09
And the documentation here.
https://github.com/phil-barrett/grblHAL-teensy-4.x/blob/master/T41U5XBB%20v207.pdf
Page16

I was planning on using the USB from the Teensy so it appears I need to cut the trace.
I also plan on using the 12 relay option and the jumper is set.

I tested that there is no continuity, but the LED next to the +5V screw terminal still lights up when I plug the USB into the Teensy.
Nothing else is plugged into the board yet.
I have built two of these and they behave the same.
What could I be missing?

phil-barrett, 2024-06-21:
Cut the trace only if you are connecting +5V to the 5V screw terminal.  If you are using USB for connectivity, there is no need for an external 5V PSU.

If you are referring to the relay outputs on the screw terminals, they operate as open collector drivers.  [Here is a blog](https://www.grbl.org/single-post/using-relays-with-grblhal-and-the-t41u5xbb) on how to use them.

[This blog](https://www.grbl.org/single-post/ttl-ssr-on-the-screw-terminals) talks about the open collector driver in some detail.

Perlovka, 2025-01-13:
After cutting the trace step motors are not running anymore, no matter if 5v or 12v is connected to screw terminal.
Motors gets enabled and I can hear sound from them, like they are trying to move, but no actual move on any axe.
Restoring trace immediately fixes the problem even when both 12v and 5v are connected.

phil-barrett, 2025-01-13:
Which trace are you cutting?  The one on the bottom of T41U5XBB?  If so, you then have to provide 5V to the boards (via the screw terminal).

Closed 2024-06-21.

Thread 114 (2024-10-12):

How to wire and configure for single_block

JasonTitcomb, 2024-10-12:
I am trying to understand how to add a toggle switch for single_block mode on the T41U5XBB.
$pins  in IO  Sender reports...
**[PIN:29 Aux in 6, Single_block]**
Can someone offer guidance?

phil-barrett, 2024-10-12:
I'm not sure how much I can help you.  Pin 29 is the Safety Door input on the T41U5XBB.  I've never tried single block mode, can you point me to any grblHAL literature on it?

JasonTitcomb, 2024-10-12:
This document lists pin 29 as the door pin.
https://github.com/phil-barrett/grblHAL-teensy-4.x/blob/master/teensy%204%20pinouts.pdf
I will try that.

JasonTitcomb, 2024-10-12:
Hi Phil,
Using the door pins would be perfect for me.
I now see [your document](https://github.com/phil-barrett/grblHAL-teensy-4.x/blob/master/teensy%204%20pinouts.pdf) stating this.

I am close to being able to try it.

It started with this issue.
https://github.com/grblHAL/core/discussions/422#discussioncomment-8062400
I am using the Web Builder and including the option "Single step G-code blocks".

phil-barrett, 2024-10-12:
Looks like you are on the cutting edge! Terje is on vacation so may not be super responsive.  Do you know how it is supposed to work? In reading up on single block for general CNC, it looks more like a mode where you hit Cycle Start, it executes one block and then goes into Feed Hold state. Is that what is supposed to happen here?

JasonTitcomb, 2024-10-12:
Yes

JasonTitcomb, 2024-10-17:
Single block works great so far.
Toggle switch is wired to the safety door by default and this works for me.
With single block enabled, each cycle start press executes just one line.
Then when confidence is high just switch single block off and cycle start to run normally.
If the job is already running and you toggle single block on then it seems to ignore it. This is fine with me.

phil-barrett, 2024-10-17:
Excellent!  I will have to play with it.  Thanks for the report.

JasonTitcomb, 2024-11-03:
Just an update to the single block feature.
It doesn't seem to honor the state of the physical switch when reset.

I cobbled together a test rig with a Arduino Due(_only because I can get the debugger working with that board_) and it seems to work correctly.
I thought it might be related to me using the safety door pin so I change.
I enabled the safety door using the web builder and that forced it to use the  B limit.
I wired my switch to the B limit on the board and it still ignores the state of the pin upon start or reset.

This is not a big deal for me as I am just a hobbyist. Just trying to report my findings for testing.
FYI I have created another issue in the grblhal repo. [https://github.com/grblHAL/iMXRT1062/issues/87](url)

phil-barrett, 2024-11-03:
Yes, I noticed that you have to cycle the switch upon reset.  Should be reported in grblHAL/core issues.

JasonTitcomb, 2024-11-04:
I believe I found the problem and created a pull request.
https://github.com/grblHAL/iMXRT1062/pull/88

Closed 2024-11-04.

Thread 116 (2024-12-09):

RE: Drivers and 3.3v VS 5.0v and Other Ideas

silver2row, 2024-12-09:
Hello...

I have had my share of 5v drivers giving me trouble. Since the teensy4.1 controller is 3.3v, look for drivers that have at least 3.3v logic associated with them like Gecko Drivers.

I got the drivers beforehand and tested them with the GRBLHal board and the Teensy4.1 add-on computer (32-bit).

Seth

P.S. This is sort of a plug but I am not associated with Gecko Drives. I just know they work and with ease because of their drivers being associated with 3.3v logic. Phew and done!

silver2row, 2024-12-09:
Also...

Is there talk of a newer board being produced? If so, I would like to get my hands on them... For instance, I say make the screw terminal headers larger for PWR and GND from the PSU to the GrblHAL board.

Seth

P.S. Just two cents here. Nothing more.

phil-barrett, 2024-12-09:
Sorry to disappoint but the driver outputs from the Teensy (and Pico) Boards are 5V.  Many drivers do not work with 3.3V.

Other that your post, I have not had a single customer complain about driver problems that were due to 5V. Please share what problems you have had. I am always interested in how I can improve the products.

silver2row, 2024-12-10:
Oh...

I use the Teensy4.1 board on the breakout you made. I am not disappointed. I just cannot get the drivers for the DM332T to understand what it is I am commanding it to do.

I got the Gecko Drivers to work, i.e. which is 3.3v to 0v min. and then 5v to 0v max.

The machine is up and running now. I always knew of the Gecko Drivers working with your breakout and the Teensy4.1 and thankfully.

I was mistaken I presume. I thought the Teensy4.1 and `T41U5XBB`, without spindle sync, used 3.3v logic.

I have been racing up and down trying to find drivers to work with your the `T41U5XBB` and Teensy4.1 because I invested in the Teensy4.1 and would like to use your boards more. There is a GND, and I am completely guessing since most driver mfg. do not Open Source their builds, on the stepper headers along with STEP/DIRECTION.

I thought the STEP/DIRECTION was a norm. It is. But...this darn driver, the DM332T, has this 5v OPTO pin that seems to give me issues. It is not them or you. It is me. I understand that the issue is mine.

Anyway...here is a quick section of the DM332T manual to better associate what I am saying with actual tech.

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

And sir, sorry to get on your bad side here. Just to repeat it, I am not disappointed with what you have built.

And yes sir, you are right. Most drivers do not work with 3.3v to 0v signals because of low switching if that is what the driver is catching.

Seth

P.S. Anyway, I understand the GND from the Stepper Screw Terminals on the `T41U5XBB` needs a way to associate a common GND with the Driver(s). The GND on the DM332T is not allocated to the pins (I/O). I am not trying to bust your bubble or ruin a good name of so-said drivers. I am just not getting why I cannot make the DM332T work with specified boards like the `T41U5XBB`. I got a Gecko Drive G251x to almost work. My shotty work on the soldering gave in...

Again. Sorry to be such a burden here. I got these drivers thinking it would be easy as cake. A cake walk. I know now it is me with the issue and I guess the support ends at that point.

Anyway, I will post a video of my creation once it is building properly. I might have to change out a motor for the Y-Axis. It is a Tronxy and it is not reacting well to my current set up.

phil-barrett, 2024-12-10:
Oops, I was wrong, you won't need to invert $2 and $3.

silver2row, 2024-12-12:
https://youtu.be/O32DJEtwVCo?si=etbbW5ISsDA59x-h

silver2row, 2024-12-12:
I got some ideas finally working. Check it out!

phil-barrett, 2024-12-12:
Super glad to hear (and see) it!  Always happy to see people getting it working together.

Phil

silver2row, 2024-12-12:
Yeppers Sir,

The machine is small for now. I plan on building a bit larger machine but for now, that is it and yes. I am glad too!

Seth

P.S. I am going to step aside from the DM332T drivers for now, i.e. as I just do not know how to use them currently. So, onto other endeavors and I will stop this thread now. Thank you again, sir.

Closed 2024-12-12.

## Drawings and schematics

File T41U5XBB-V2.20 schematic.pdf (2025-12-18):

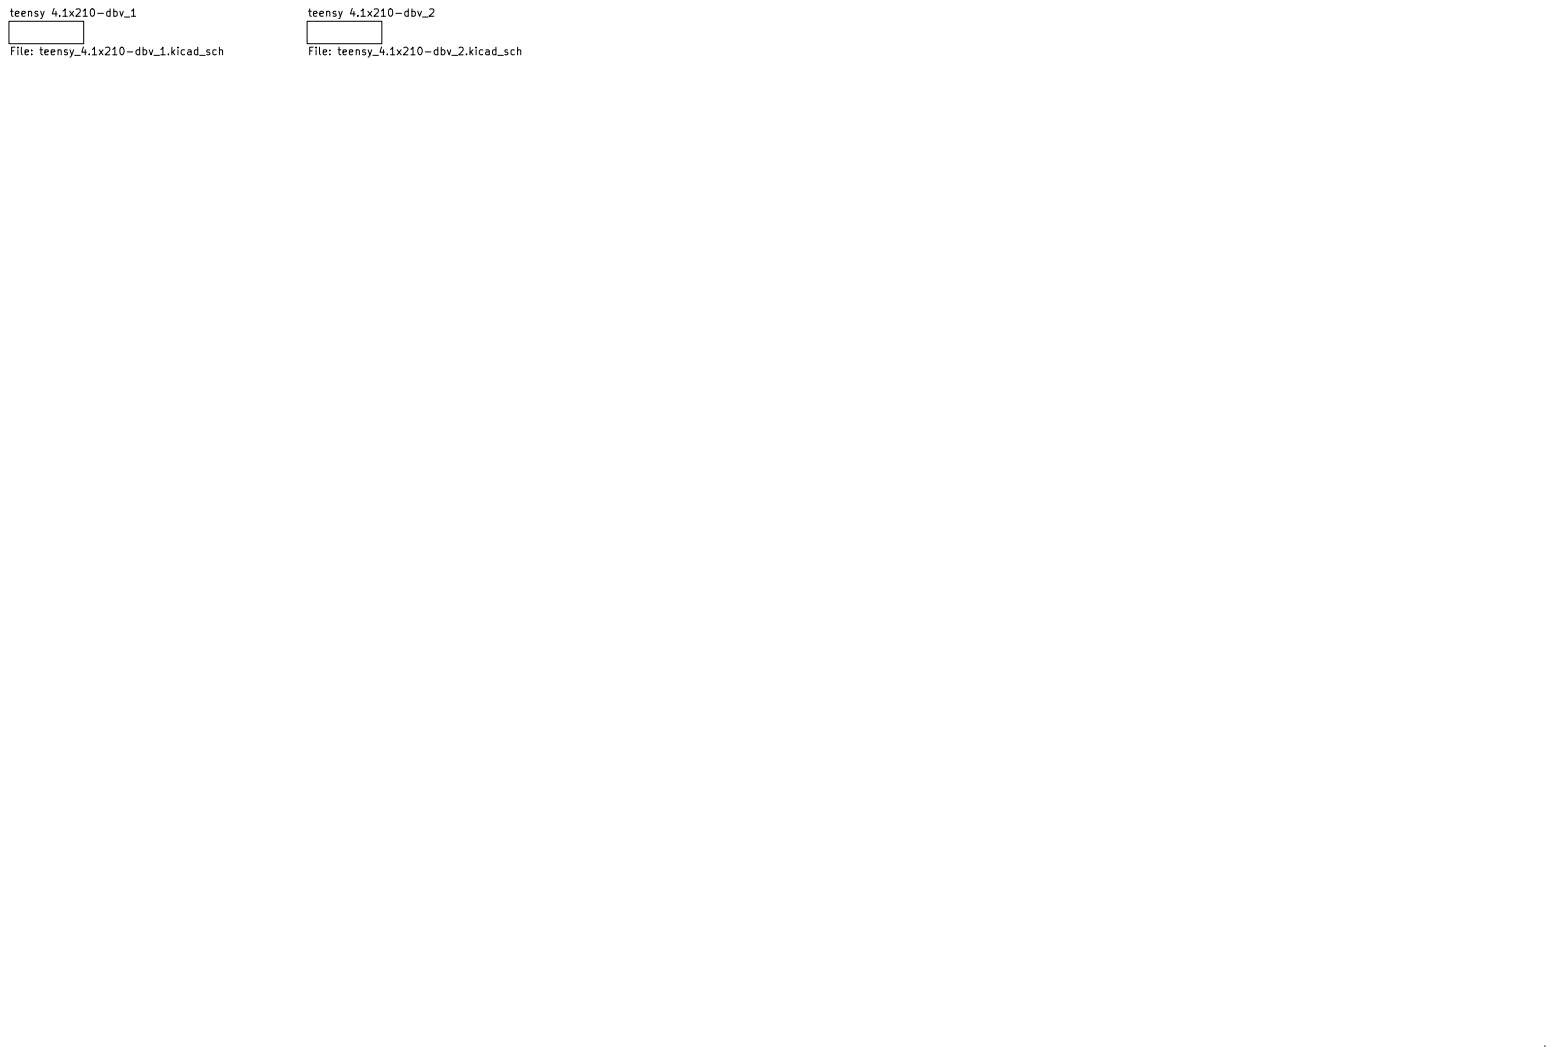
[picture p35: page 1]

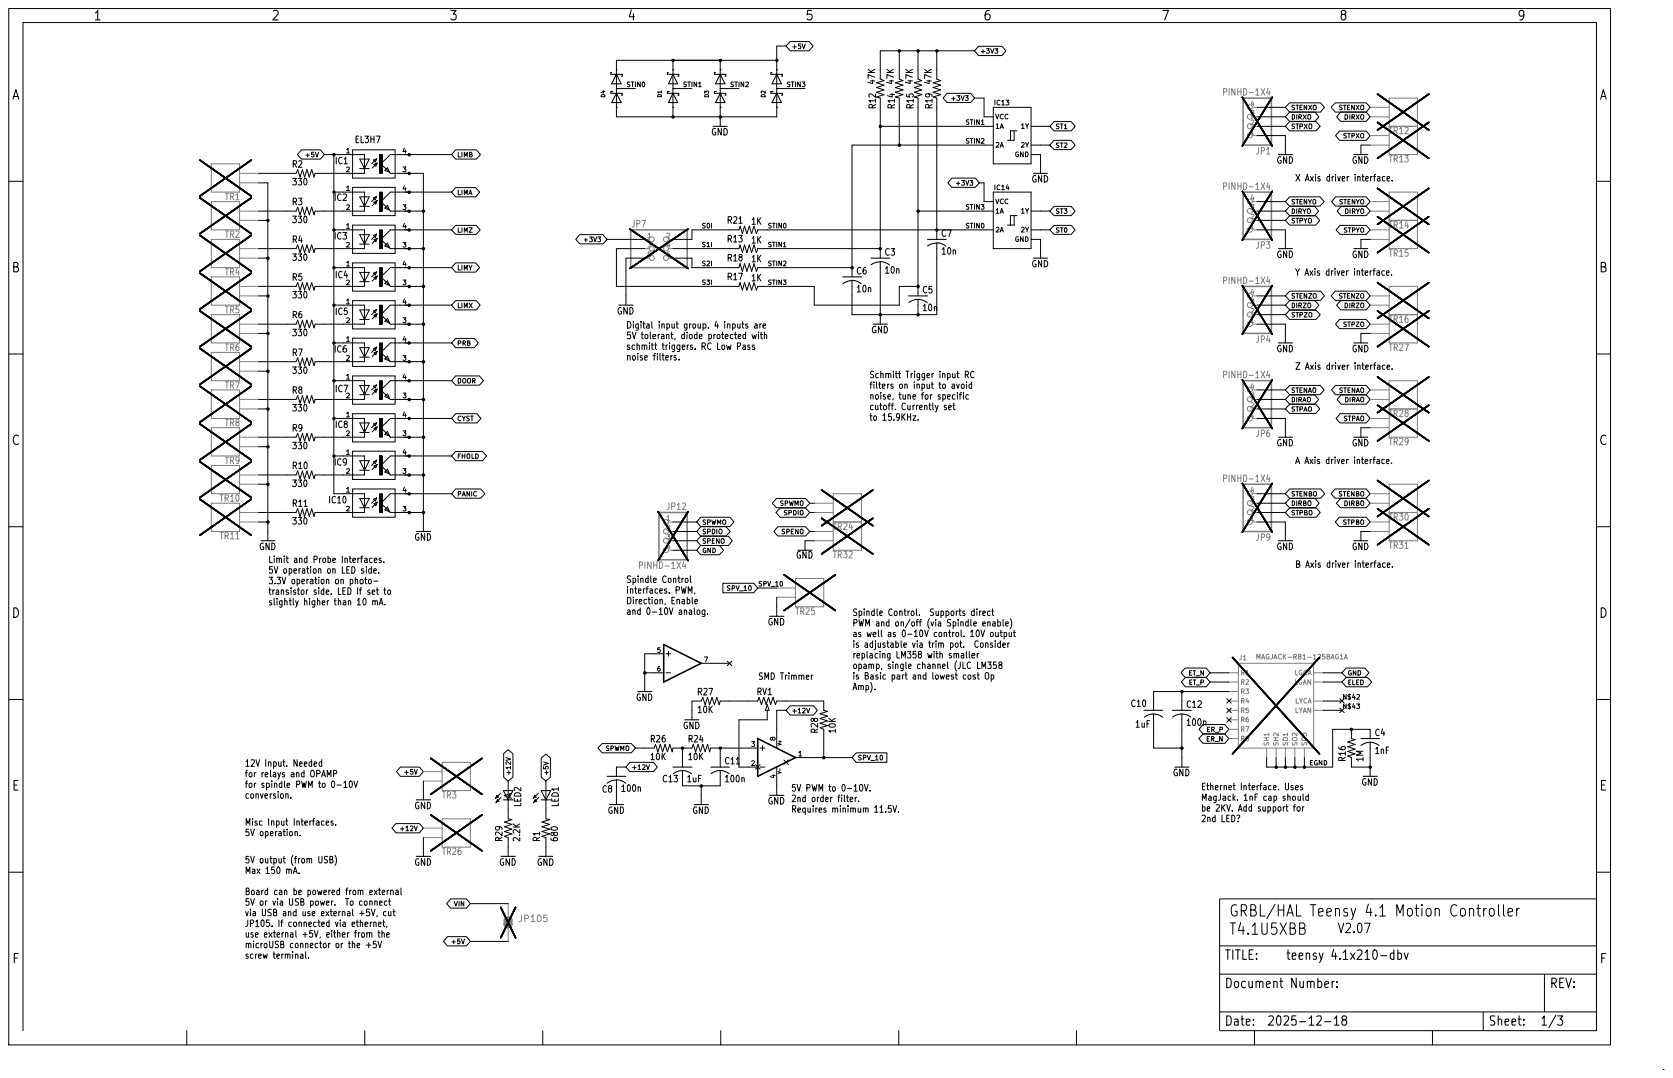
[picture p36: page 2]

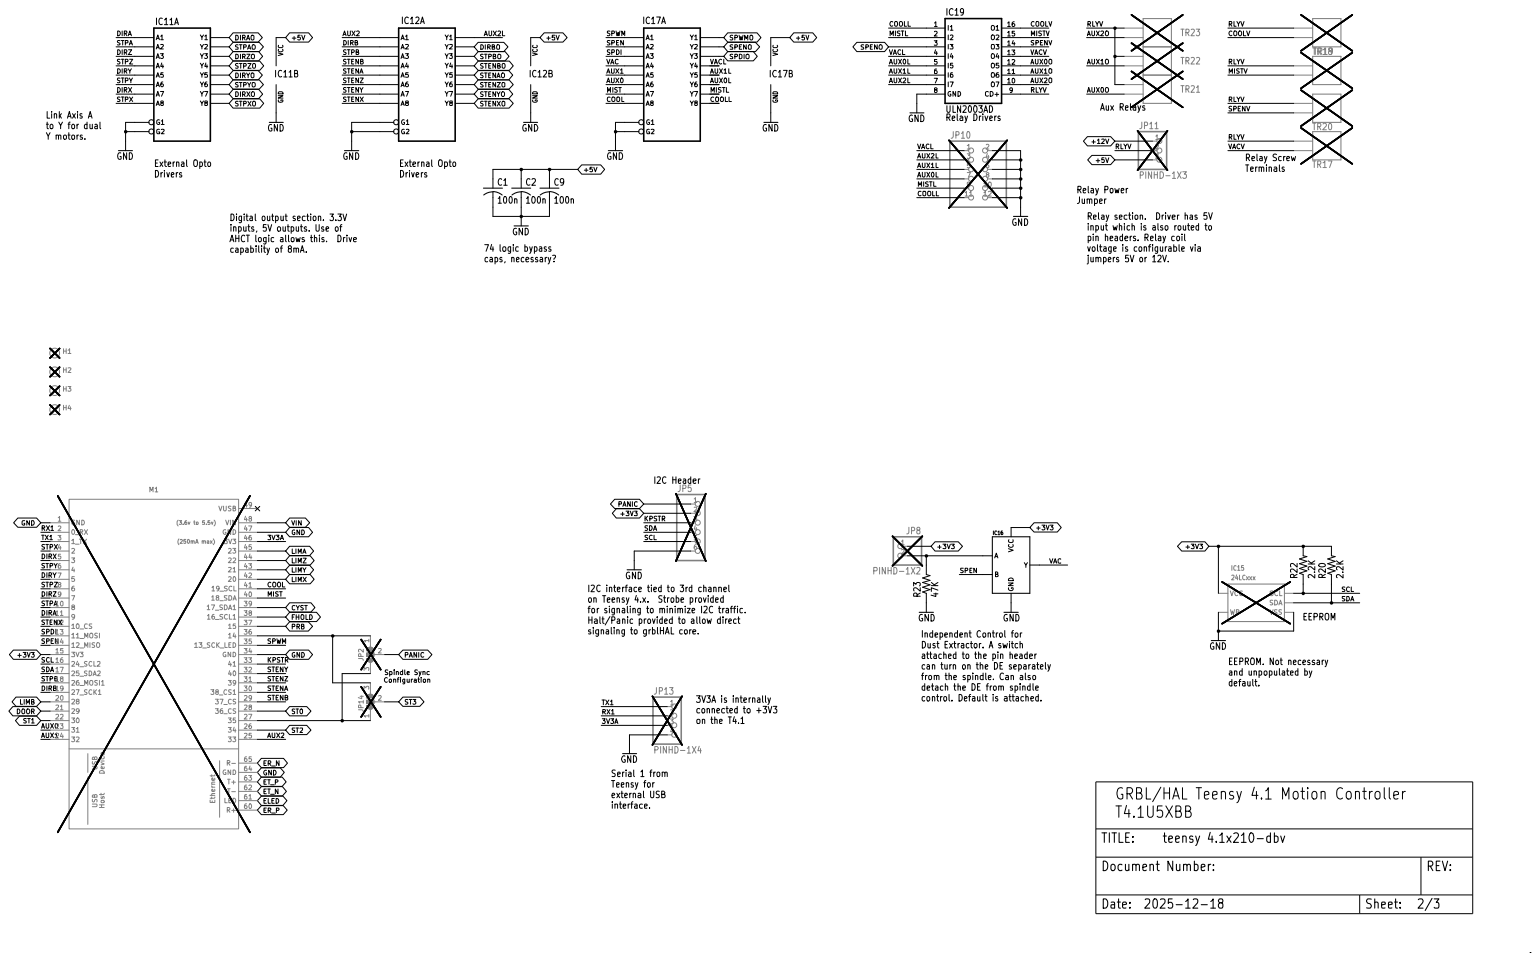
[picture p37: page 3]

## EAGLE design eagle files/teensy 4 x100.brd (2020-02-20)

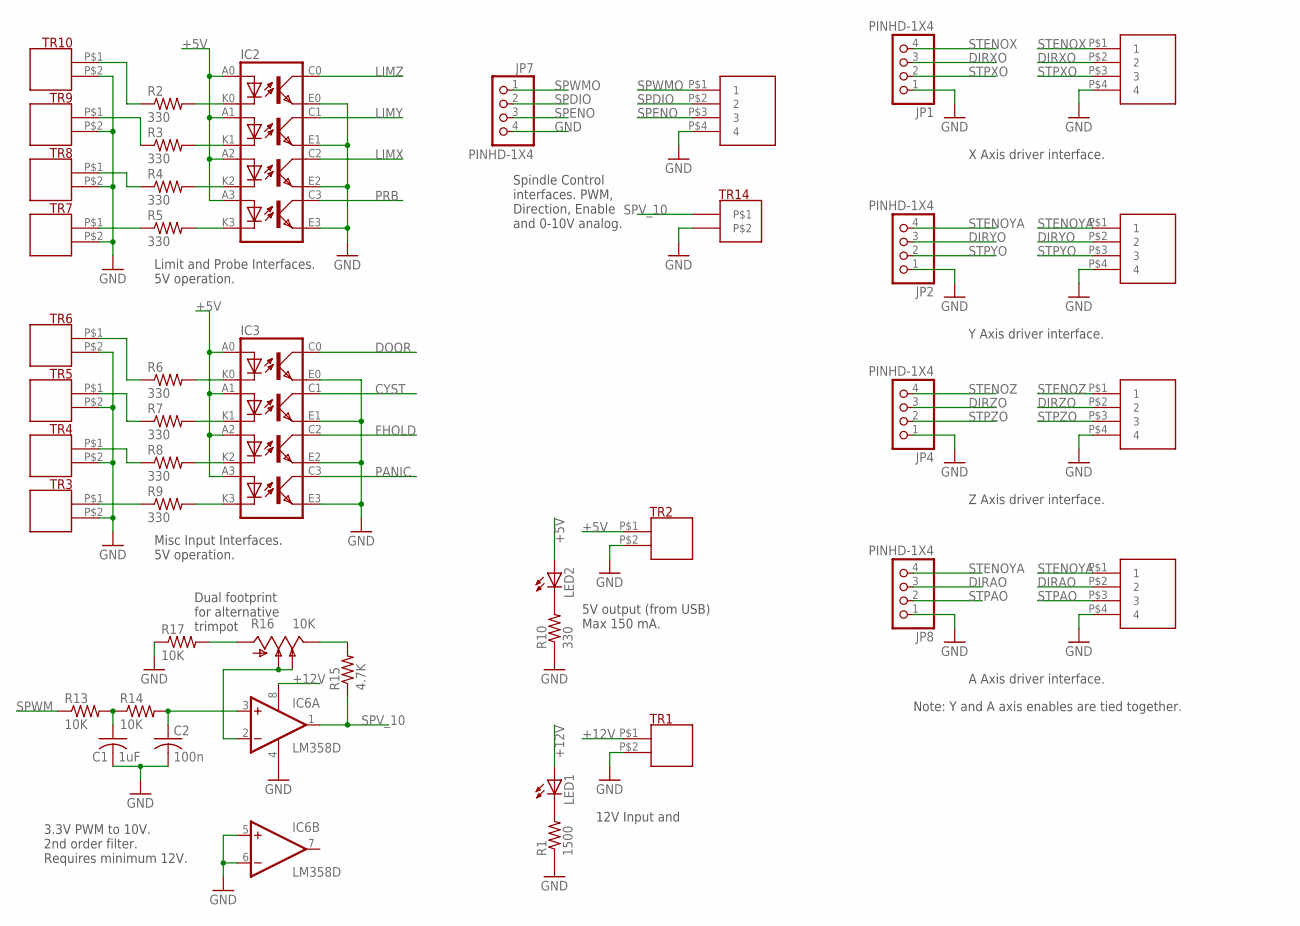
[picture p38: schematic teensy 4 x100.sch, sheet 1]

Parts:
C1: 1uF; C1206
C2: 100n; C1206
IC2, IC3: LTV846S; DIL16-SMD
IC6: LM358D; SO08
JP1, JP2, JP4, JP7, JP8: PINHD-1X4; 1X04
LED1, LED2: LED3MM
R1: 1500; R1206
R2, R3, R4, R5, R6, R7, R8, R9, R10: 330; R1206
R13, R14, R17: 10K; R1206
R15: 4.7K; R1206
R16: 10K; B64Y
TR1, TR2, TR3, TR4, TR5, TR6, TR7, TR8, TR9, TR10, TR14: T35-2
TR11, TR12, TR13, TR19, TR20: T35-4

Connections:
+5V: IC2.A0, IC2.A1, IC2.A2, IC2.A3, IC3.A0, IC3.A1, IC3.A2, IC3.A3, LED2.A, TR2.P$1; also elsewhere on the board
+12V: IC6.8 (V+), LED1.A, TR1.P$1; also elsewhere on the board
CYST: IC3.C1 (COL1); also elsewhere on the board
DIRAO: JP8.3, TR20.P$2 (2); also elsewhere on the board
DIRXO: JP1.3, TR11.P$2 (2); also elsewhere on the board
DIRYO: JP2.3, TR12.P$2 (2); also elsewhere on the board
DIRZO: JP4.3, TR13.P$2 (2); also elsewhere on the board
DOOR: IC3.C0 (COL0); also elsewhere on the board
FHOLD: IC3.C2 (COL2); also elsewhere on the board
GND: C1.2, C2.2, IC2.E0 (EMIT0), IC2.E1 (EMIT1), IC2.E2 (EMIT2), IC2.E3 (EMIT3), IC3.E0 (EMIT0), IC3.E1 (EMIT1), IC3.E2 (EMIT2), IC3.E3 (EMIT3), IC6.4 (V-), IC6.5 (+IN), IC6.6 (-IN), JP1.1, JP2.1, JP4.1, JP7.4, JP8.1, R1.1, R10.1, R17.1, TR1.P$2, TR2.P$2, TR3.P$2, TR4.P$2, TR5.P$2, TR6.P$2, TR7.P$2, TR8.P$2, TR9.P$2, TR10.P$2, TR11.P$4 (4), TR12.P$4 (4), TR13.P$4 (4), TR14.P$2, TR19.P$4 (4), TR20.P$4 (4); also elsewhere on the board
LIMX: IC2.C2 (COL2); also elsewhere on the board
LIMY: IC2.C1 (COL1); also elsewhere on the board
LIMZ: IC2.C0 (COL0); also elsewhere on the board
unnamed: IC3.K0 (C0), R6.2
unnamed: LED2.K (C), R10.2
unnamed: IC3.K1 (C1), R7.2
unnamed: LED1.K (C), R1.2
unnamed: IC3.K2 (C2), R8.2
unnamed: IC2.K0 (C0), R2.2
unnamed: IC2.K1 (C1), R3.2
unnamed: IC2.K2 (C2), R4.2
unnamed: IC2.K3 (C3), R5.2
unnamed: IC3.K3 (C3), R9.2
unnamed: C1.1, R13.2, R14.1
unnamed: C2.1, IC6.3 (+IN), R14.2
unnamed: R15.2, R16.E
unnamed: IC6.2 (-IN), R16.S, R16.S1
unnamed: R16.A, R17.2
unnamed: R2.1, TR10.P$1
unnamed: R3.1, TR9.P$1
unnamed: R4.1, TR8.P$1
unnamed: R5.1, TR7.P$1
unnamed: R6.1, TR6.P$1
unnamed: R7.1, TR5.P$1
unnamed: R8.1, TR4.P$1
unnamed: R9.1, TR3.P$1
PANIC: IC3.C3 (COL3); also elsewhere on the board
PRB: IC2.C3 (COL3); also elsewhere on the board
SPDIO: JP7.2, TR19.P$2 (2); also elsewhere on the board
SPENO: JP7.3, TR19.P$3 (3); also elsewhere on the board
SPV_10: IC6.1 (OUT), R15.1, TR14.P$1
SPWM: R13.1; also elsewhere on the board
SPWMO: JP7.1, TR19.P$1 (1); also elsewhere on the board
STENOX: JP1.4, TR11.P$1 (1); also elsewhere on the board
STENOYA: JP2.4, JP8.4, TR12.P$1 (1), TR20.P$1 (1); also elsewhere on the board
STENOZ: JP4.4, TR13.P$1 (1); also elsewhere on the board
STPAO: JP8.2, TR20.P$3 (3); also elsewhere on the board
STPXO: JP1.2, TR11.P$3 (3); also elsewhere on the board
STPYO: JP2.2, TR12.P$3 (3); also elsewhere on the board
STPZO: JP4.2, TR13.P$3 (3); also elsewhere on the board

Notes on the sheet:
Dual footprint for alternative trimpot
Limit and Probe Interfaces. 5V operation.
Misc Input Interfaces. 5V operation.
Spindle Control interfaces. PWM, Direction, Enable and 0-10V analog.
3.3V PWM to 10V. 2nd order filter. Requires minimum 12V.
5V output (from USB) Max 150 mA.
12V Input and
X Axis driver interface.
Y Axis driver interface.
Z Axis driver interface.
A Axis driver interface.
Note: Y and A axis enables are tied together.

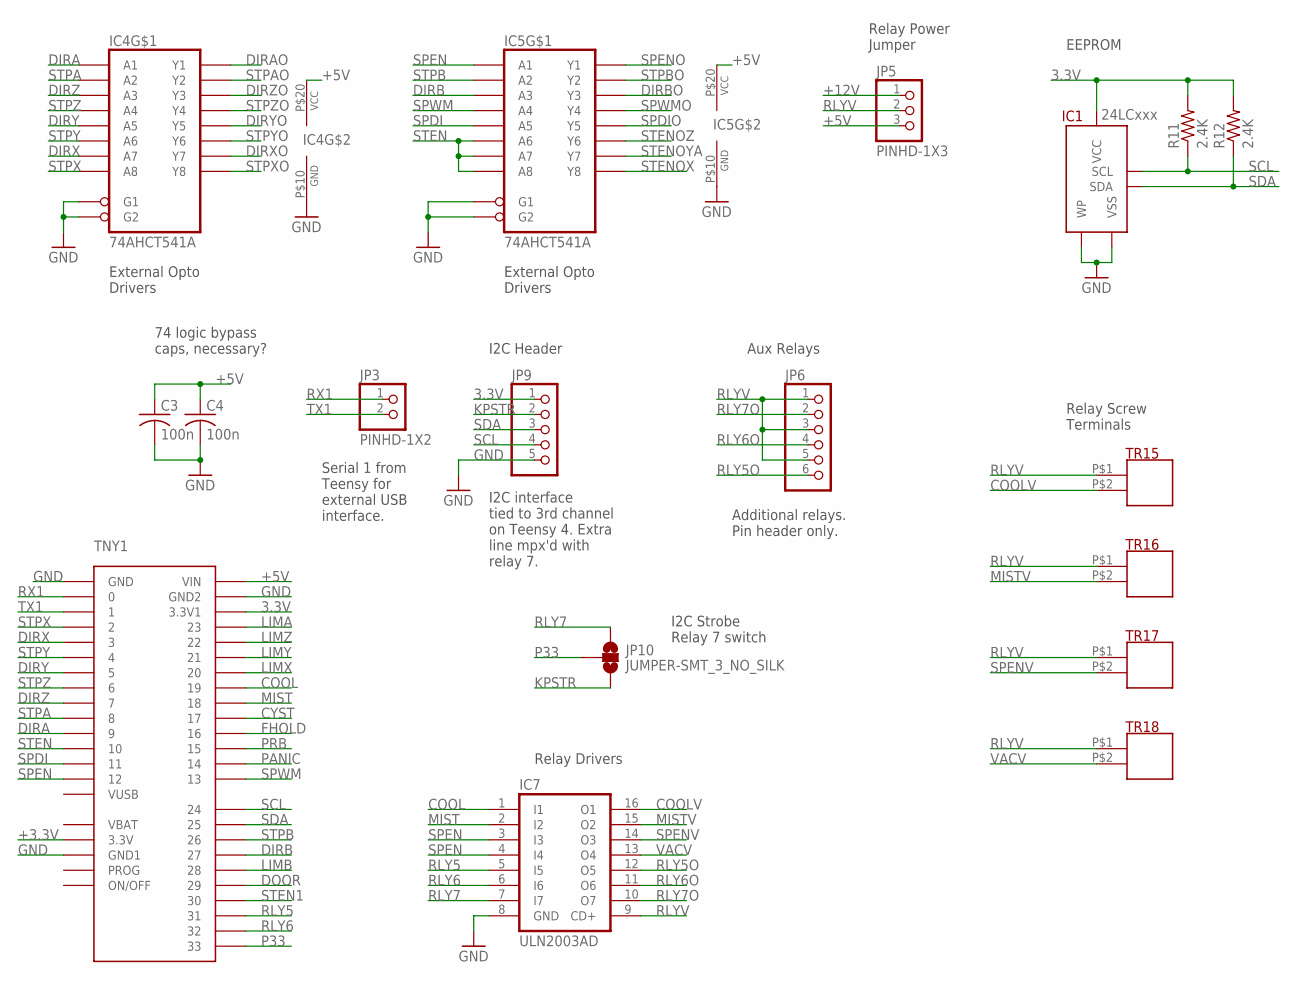
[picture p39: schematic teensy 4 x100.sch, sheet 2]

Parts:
C3, C4: 100n; C1206
IC1: 24LCxxx; SOIC-8(MICROCHIP)
IC4, IC5: 74AHCT541A; TSSOP20
IC7: ULN2003AD; SO16
JP3: PINHD-1X2; 1X02
JP5: PINHD-1X3; 1X03
JP6: PINHD-1X6; 1X06
JP9: PINHD-1X5; 1X05
JP10: JUMPER-SMT_3_NO_SILK; SMT-JUMPER_3_NO_SILK
R11, R12: 2.4K; R1206
TNY1: TEENSY4.0
TR15, TR16, TR17, TR18: T35-2

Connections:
3.3V: IC1.P$8 (VCC), JP9.1, R11.2, R12.2, TNY1.3.31 (3.3V1)
+3.3V: TNY1.3.30 (3.3V)
+5V: C3.1, C4.1, IC4.P$20 (VCC), IC5.P$20 (VCC), JP5.3, TNY1.VIN; also elsewhere on the board
+12V: JP5.1; also elsewhere on the board
COOL: IC7.1 (I1), TNY1.19
COOLV: IC7.16 (O1), TR15.P$2
CYST: TNY1.17; also elsewhere on the board
DIRA: IC4.P$2 (A1), TNY1.9
DIRAO: IC4.P$18 (Y1); also elsewhere on the board
DIRB: IC5.P$4 (A3), TNY1.27
DIRBO: IC5.P$16 (Y3)
DIRX: IC4.P$8 (A7), TNY1.3
DIRXO: IC4.P$12 (Y7); also elsewhere on the board
DIRY: IC4.P$6 (A5), TNY1.5
DIRYO: IC4.P$14 (Y5); also elsewhere on the board
DIRZ: IC4.P$4 (A3), TNY1.7
DIRZO: IC4.P$16 (Y3); also elsewhere on the board
DOOR: TNY1.29; also elsewhere on the board
FHOLD: TNY1.16; also elsewhere on the board
GND: C3.2, C4.2, IC1.P$4 (VSS), IC1.P$7 (WP), IC4.P$1 (G1), IC4.P$10 (GND), IC4.P$19 (G2), IC5.P$1 (G1), IC5.P$10 (GND), IC5.P$19 (G2), IC7.8 (GND), JP9.5, TNY1.GND, TNY1.GND1, TNY1.GND2; also elsewhere on the board
KPSTR: JP9.2, JP10.3
LIMA: TNY1.23
LIMB: TNY1.28
LIMX: TNY1.20; also elsewhere on the board
LIMY: TNY1.21; also elsewhere on the board
LIMZ: TNY1.22; also elsewhere on the board
MIST: IC7.2 (I2), TNY1.18
MISTV: IC7.15 (O2), TR16.P$2
P33: JP10.2, TNY1.33
PANIC: TNY1.14; also elsewhere on the board
PRB: TNY1.15; also elsewhere on the board
RLY5: IC7.5 (I5), TNY1.31
RLY5O: IC7.12 (O5), JP6.6
RLY6: IC7.6 (I6), TNY1.32
RLY6O: IC7.11 (O6), JP6.4
RLY7: IC7.7 (I7), JP10.1
RLY7O: IC7.10 (O7), JP6.2
RLYV: IC7.9 (CD+), JP5.2, JP6.1, JP6.3, JP6.5, TR15.P$1, TR16.P$1, TR17.P$1, TR18.P$1
RX1: JP3.1, TNY1.0
SCL: IC1.P$6 (SCL), JP9.4, R11.1, TNY1.24
SDA: IC1.P$5 (SDA), JP9.3, R12.1, TNY1.25
SPDI: IC5.P$6 (A5), TNY1.11
SPDIO: IC5.P$14 (Y5); also elsewhere on the board
SPEN: IC5.P$2 (A1), IC7.3 (I3), IC7.4 (I4), TNY1.12
SPENO: IC5.P$18 (Y1); also elsewhere on the board
SPENV: IC7.14 (O3), TR17.P$2
SPWM: IC5.P$5 (A4), TNY1.13; also elsewhere on the board
SPWMO: IC5.P$15 (Y4); also elsewhere on the board
STEN: IC5.P$7 (A6), IC5.P$8 (A7), IC5.P$9 (A8), TNY1.10
STEN1: TNY1.30
STENOX: IC5.P$11 (Y8); also elsewhere on the board
STENOYA: IC5.P$12 (Y7); also elsewhere on the board
STENOZ: IC5.P$13 (Y6); also elsewhere on the board
STPA: IC4.P$3 (A2), TNY1.8
STPAO: IC4.P$17 (Y2); also elsewhere on the board
STPB: IC5.P$3 (A2), TNY1.26
STPBO: IC5.P$17 (Y2)
STPX: IC4.P$9 (A8), TNY1.2
STPXO: IC4.P$11 (Y8); also elsewhere on the board
STPY: IC4.P$7 (A6), TNY1.4
STPYO: IC4.P$13 (Y6); also elsewhere on the board
STPZ: IC4.P$5 (A4), TNY1.6
STPZO: IC4.P$15 (Y4); also elsewhere on the board
TX1: JP3.2, TNY1.1
VACV: IC7.13 (O4), TR18.P$2

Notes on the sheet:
I2C Header
Aux Relays
Relay Power Jumper
EEPROM
Relay Screw Terminals
Relay Drivers
I2C Strobe Relay 7 switch
External Opto Drivers
74 logic bypass caps, necessary?
Serial 1 from Teensy for external USB interface.
I2C interface tied to 3rd channel on Teensy 4. Extra line mpx'd with relay 7.
Additional relays. Pin header only.

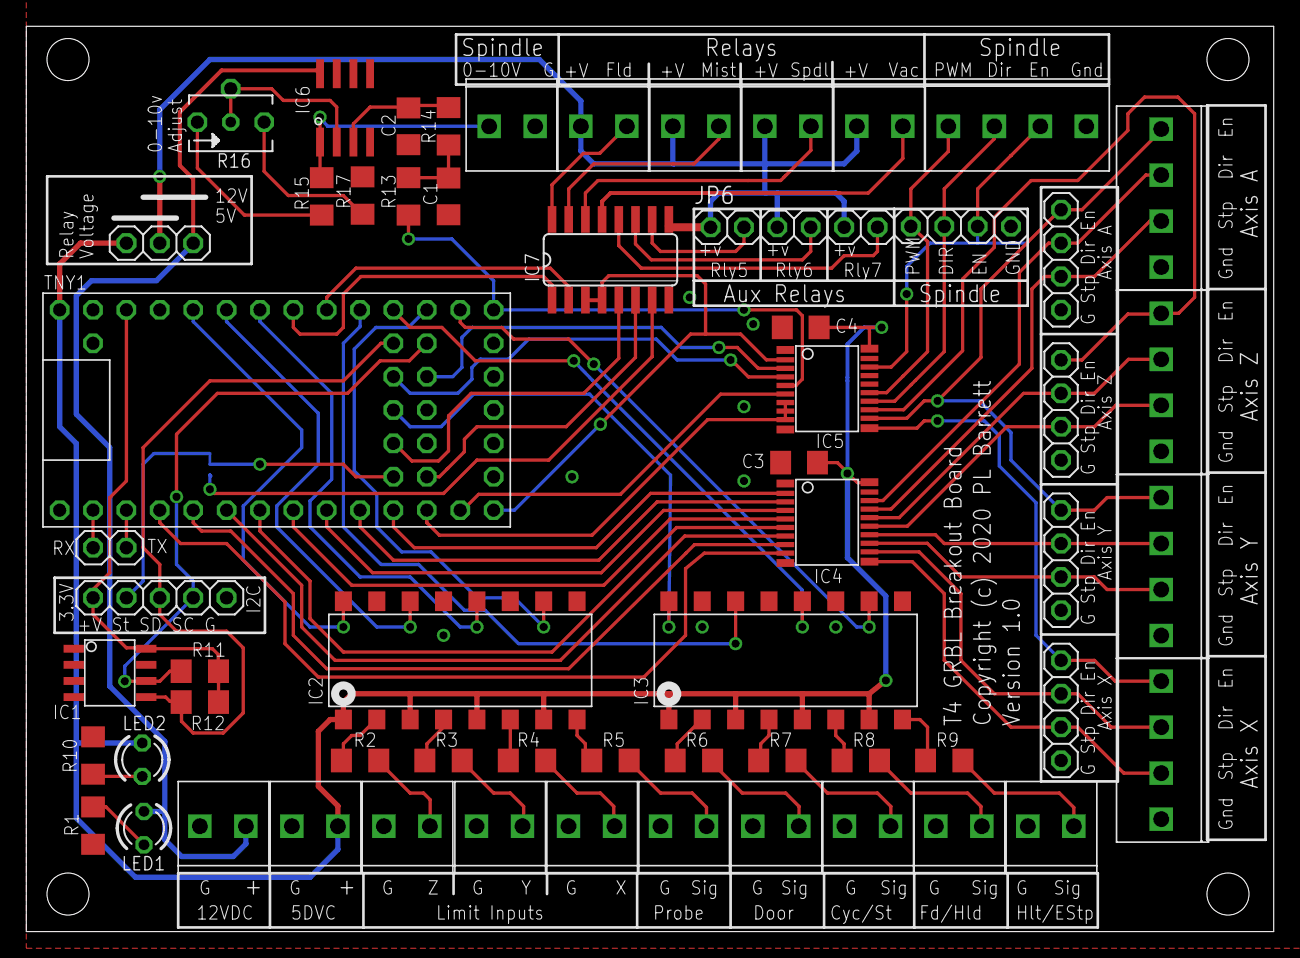
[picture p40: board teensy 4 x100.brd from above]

Board: 2 copper layers, 94.9 x 68.9 mm, 61 parts (1 on the bottom side), 83 nets.

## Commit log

2020-02-18 Added schematic
    [teensy 4 layout.xls]
2020-02-18 added eagle sch and brd files
    [teensy 4 x100.brd, teensy 4 x100.sch]
2020-02-19 Add files via upload
    fix to stepper enable lines
    [teensy 4 x100.brd]
2020-02-19 Add files via upload
    Added i2c header and a few trace cleanups.
2020-02-19 Add files via upload
    Added i2c header, trace clean up.
    [teensy 4 x100.brd, teensy 4 x100.sch]
2020-02-19 Add files via upload
    PCB traces. Red is top, blue is bottom.
2020-02-19 Add files via upload
    Ver .2 Made alternate pin assignments more clear in the table. Swapped Spindle PWM and Spindle Enable pins to put PWM on the LED pin for a visual spindle diagnostic.
2020-02-20 Add files via upload
    Minor changes to Spindle pin assignments.
    [teensy 4 x100.brd, teensy 4 x100.sch]
2020-02-20 Add files via upload
    Changed spindle pin assignments, in line with the Teensy 4 Pinouts PDF
    [teensy 4 x100.brd, teensy 4 x100.sch]
2020-02-20 Add files via upload
    Update circuit to reflect moving spindle PWM to pin 13 and Spindle enable to Pin 12.
2020-03-01 Delete teensy 4 x100.csv
    replacing with official BOM
    [teensy 4 x100.csv]
2020-03-07 Photo of V1.00 board
2020-06-28 Add files via upload
    New version based on Teensy 4.1.
2020-07-06 Add V2.05 Schematic
    V2.05 Schematic.
2020-07-06 Update for grblHAL build guide
2020-10-27 Updated incorrect 24 pin socket part number.
2020-11-08 Ethernet Configurations
    TEENSY41_3X_ETH_ENC.hex --- 3 Axis, ethernet, encoder.
    TEENSY41_3XGY_ETH_ENC.hex --- 3 Axis, B Axis ganged to Y, ethernet, encoder.
    TEENSY41_4X_ETH_ENC.hex --- 4 Axis, ethernet, encoder.
    TEENSY41_4XGY_ETH_ENC.hex --- 4 Axis, B Axis ganged to Y, ethernet, encoder.
    TEENSY41_5X_ETH_ENC.hex --- 5 Axis, ethernet, encoder.
2020-11-20 Updated assembly info for Ethernet
2020-12-01 Added 2x3 2mm socket and header part numbers
2021-02-10 grblHAL binaries with planning buffer increase to 1024.
2021-02-12 Depreciated in favor grblHAL Wiki
2021-02-24 Eagle Schematic for V2.09.
2021-12-02 Replaced grblHAL_T41E3XGYAS.hex with correct number of axes
2021-12-17 T41U5XBB V 2.09 STEP file - experimental.
    KiCAD import, used to generate STEP file. Not verified.
2022-01-03 Updated to newer builds of grblHAL
2022-10-11 Add files via upload
    Teensy 4.0 breakout board.
2023-01-27 Add files via upload
    Common T41U5XBB firmware configuration files for use with the grblHAL Web Builder.

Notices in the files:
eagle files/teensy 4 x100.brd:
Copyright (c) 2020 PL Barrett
